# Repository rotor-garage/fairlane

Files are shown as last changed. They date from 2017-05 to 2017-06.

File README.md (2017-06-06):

# Fairlane

The Fairlaine is an ```R``` designed 215mm motor to motor 5" racing and freestyle frame.

>Presence of this frame is said to warm a thousand motors and without effort fascinate the soul and want to go faster. The cheerful and playful potential animates all that are fortunate enough to encounter footage of a flight. 

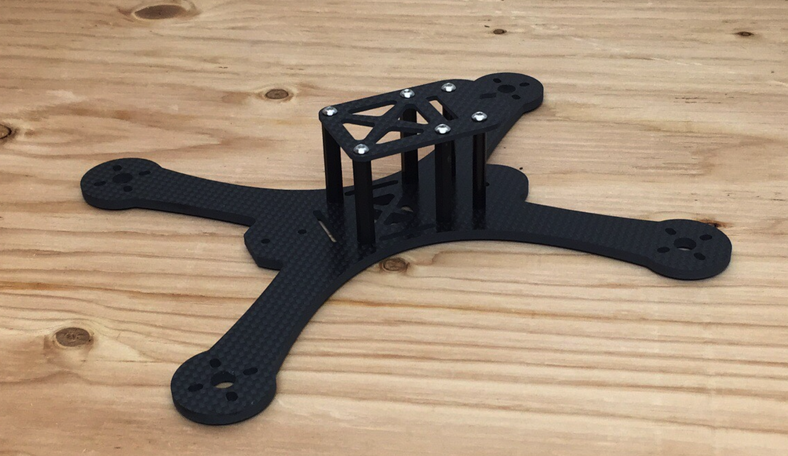
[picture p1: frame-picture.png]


Specification:
* 215mm mtm "stretch" frame
* Nominal 1.25:1 ratio (L:W)
* Under 600g AUW racing, 600-750g freestyle (depending on HD cam)
* 22xx motors
* 5 inch props
* 30.5mm FC mount (KISS, CF/BF, etc)
* Underslung battery, single strap
* 20-35mm standoff depending on components and build
* Fits HS1177 type flight camera

### Target Pilot

Medium or greater experience. Not the best first build but also not the hardest by any means. The Fairlane is fast and once tuned horizontal and vertical acceleration is thrilling. When performing freestyle with high rates the Fairlane sounds like a knife fight in the sky.

### Building the Fairlane

* The frame design requires a good control of wires, length, and direct connection (solder not bullets). 
* ESCs are mounted on the arms as per the builders preference.
* The flight controller is center mounted and can be fastened using bolts or plastic means. Both spacers and standoff stacks are possible in material and format of choice.
* The top plate attaches via standoff (20 to 35mm is common) and is provided to yield tight support for common cameras (GoPro, Mobius, Runcam, etc).
	* Mounting is a per-camera operation, but Creative Dex type mounts work fine
* 4s 1300-1800mah recommended. 3s is also good, just less voltage and the same mah.
* Stack mounted PDB is recommended
* VTX 
	* Mount under top plate easily, other mounting options are available on a per build basis
	* Racing/vertical mount possible, depends on standoff height and vtx
	* Stack VTX is fine. Beware EM and stack height issues
	* Top of top plate not a recommended mount
	* Right angle antenna connection suggested (pigtail/strait also compatible)
	* FX79* form factor is an easy fit
* Camera (HS1177 form) allows 20 to 45+ degree

## Parts List:

* Mechanical (minimal, frame only)
	* __Frame only__
		* 4x 3mm bolt 25-40mm for the stack
		* 8x or more 3mm+ inside diameter spacers (for between stack items as your stack dictates)
		* 4x nylon or nylon lock nut (cap the stack
		* 4x 20-35mm standoff (as your stack dictates)
		* 8x 3x6mm (or longer) screws to mate with standoff
* __Notes:__
	* 3mm frame supports 6mm length screws (motor mount, etc)
	* 4mm frame supports 8mm length screws (motor mount, etc)
	* Length of motor mount screws will vary based on the design of equipment so pay attention
		* _Metric socket button head screws are always recommended_
* Electrical
	* 1x Flight controller
	* 1x PDB
	* 1x Flight camera
	* 4x Electronic speed control (20amp minimum)
	* 4x Motor 22xx 2000-2700kv range
		* 16x 3x6 or larger mount screws
		* 4x prop nuts
	* 4x+ props
	* VTX
	* VTX antenna
	* RC Radio transmitter and receiver
	* FPV goggles with receiver
	* OSD recommended
	* Wire, solder, flux, lock-tite
* Skills
	* Have them
	* Use them
	* Stay tight
	
## Where to get this unit?

Visit http://rotorgarage.com or send an email to info [at] rotorgarage [dot] com

## Open Source

This work is provided open source using the following license:

Attribution-NonCommercial-ShareAlike 4.0 International (CC BY-NC-SA 4.0)

More information here https://creativecommons.org/licenses/by-nc-sa/4.0/

License Summary:

>This license lets you to remix, tweak, and build upon the work non-commercially, as long as credit is provided to Rotor Garage and license the creation under the identical terms.

## Need more?

If you would like to license this design please send an email to info [at] rotorgarage [dot] com explaining your desire and details on the production and/or use. We are more than happy to issue commercial licenses and continue growing our partnerships.

Rotor Garage:

* Web: http://rotorgarage.com
* Email: info [at] rotorgarage [dot] com
* Twitter: [@rotorgarage](http://twitter.com/rotorgarage)
* Instagram: [@rotorgarage](http://instagram.com/rotorgarage)
* [Facebook page](https://www.facebook.com/Rotor-Garage-368713813495485/)
* Github: https://github.com/rotor-garage

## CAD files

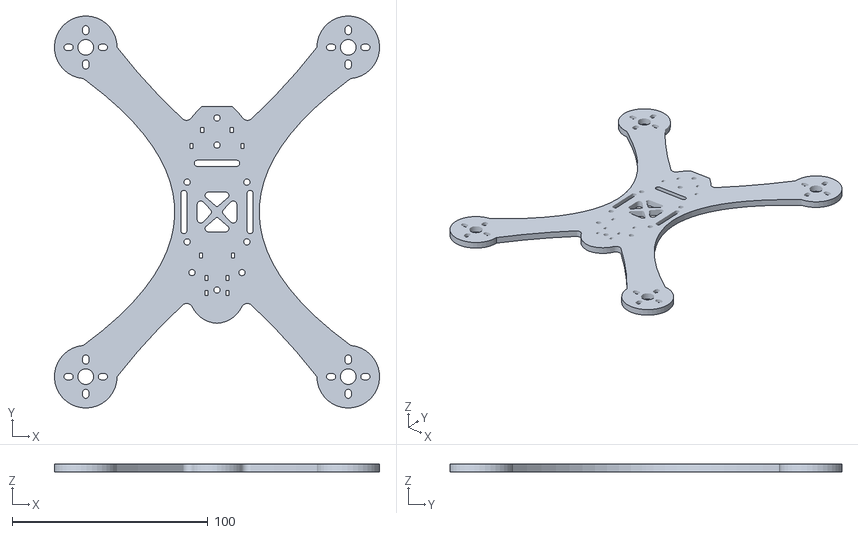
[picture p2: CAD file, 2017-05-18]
frame/R-215.STL
165.9 x 200.1 x 4.00

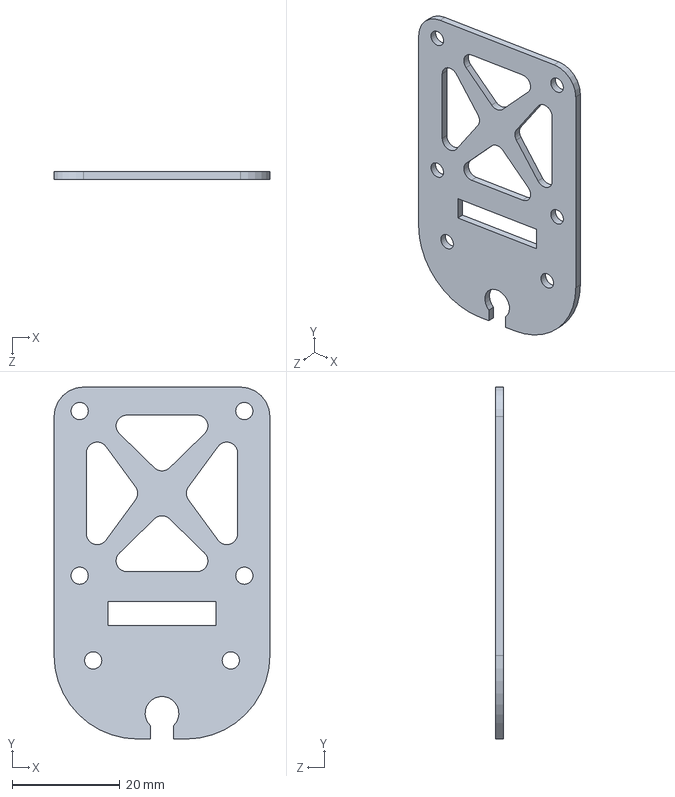
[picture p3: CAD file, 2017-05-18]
top-plate/R-215 Top Plate.SLDPRT
40.0 x 65.2 x 1.50 mm

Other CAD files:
frame/R-215.DXF
top-plate/R-215 Top Plate.DXF
top-plate/R-215 Top Plate.STL

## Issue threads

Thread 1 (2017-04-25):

Widen FC mount holes

datamafia, 2017-04-25:
Currently the FC is 30mm (KISS) and we need 30.5mm to support majority stack PCBs.

Mr-A-Designs, 2017-05-08:
Widen the rear standoff spacing for access to USB ports that are in the stack. Both base and top plate hole spacing. (Diatone SP3 VTX)

datamafia, 2017-05-23:
FC fixed in 328292c07de3c460b28aa764275290e718292aa9. Moving second comment to separate issue.

Closed 2017-05-23.

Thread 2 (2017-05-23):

Rear stand off adjustment

datamafia, 2017-05-23:
Pulled from Issue #1

Widen the rear standoff spacing for access to USB ports that are in the stack. Both base and top plate hole spacing. (Diatone SP3 VTX) Current 10.75 mm from center line.

datamafia, 2017-05-23:
@Mr-A-Designs -- I can't confirm this locally right now, but I did run a check on the top and bottom plate holes matching for production run.  I will keep this open until I can measure old and new frames for this point.

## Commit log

2017-04-25 Initial commit
    We are aware that the FC mount holes are KISS only. Pending fix.
    [R-215 Top Plate.DXF, R-215 Top Plate.SLDPRT, R-215 Top Plate.STL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]
2017-05-18 Version 2 changes
    Flight controller 30.5mm spacing
    [R-215 Top Plate.DXF, R-215 Top Plate.SLDPRT, R-215 Top Plate.STL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]
2017-06-06 adding frame picture to try and link in readme
